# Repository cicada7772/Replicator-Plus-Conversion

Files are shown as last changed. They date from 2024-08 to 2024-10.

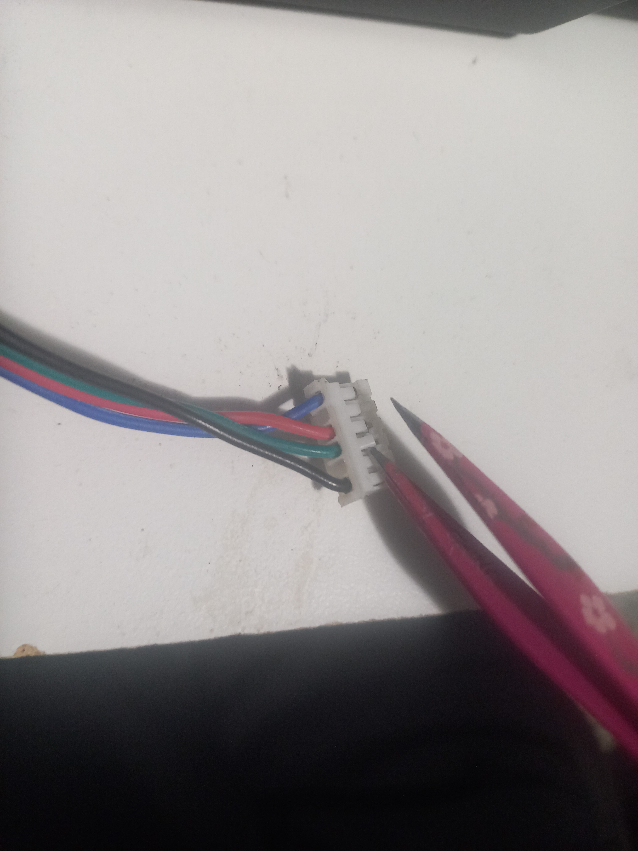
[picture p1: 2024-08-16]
Images/IMG_20240813_204058.jpg

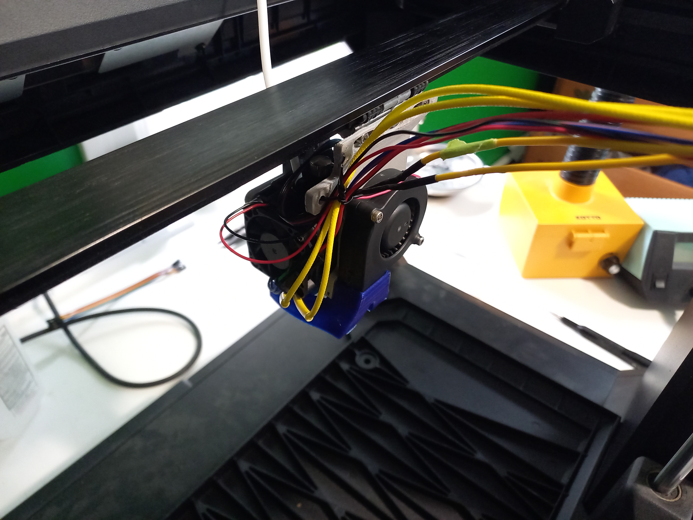
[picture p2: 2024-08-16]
Images/IMG_20240816_153703.jpg

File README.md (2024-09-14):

## Replicator Plus Conversion
This project converts a Makerbot Replicator Plus into a standard, reliable, and fast machine. 

The design goals of this project are:
* Increased reliability
* Use of standard parts
* Minimal disassembly
* Keeping the build process as simple as possible
* Keeping the budget low
* Thorough assembly instructions

Check out the wiki of this repo for details here:
https://github.com/cicada7772/ReplicatorPlusConversion/wiki

Some similar projects:

* https://github.com/mikedaf/Makerbot-Replicator-Plus-Klipper-Conversion
* https://github.com/rolohaun/Replicator5-Klipper

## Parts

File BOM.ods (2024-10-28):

 | ITEM | QTY | Price (USD)
Replicator++
Components | E3D Hemera XS Extruder --> Direct, 12V ← ( SKU:HEMERA-XS-175-COLD-D-12V) | 1 | 127.22
 | E3D Revo Starter Hotside Packs → 12V, 104NT ← (SKU:REVO-HOT-KIT-12V) | 1 | 51.93
 | BTT SKR MINI E3 V3.0 mainboard | 1 | 33.98
 | BL-touch style probe (ex: BIQU Microprobe V2.0) (recommended) | 1 | 18.99
 |  |  | 232.12 | ← Total(USD)
Materials | AWG16 stranded wire | x
 | AWG22 stranded wire | x
 | Stepper cables (1 meter) | 3
 | M3*4 SHCS | 8
 | M3*20 SHCS | 4
 | M3*8 SHCS | 3
 | M3*5 SHCS | 4
 | M3 Hexnuts | 2
Replicator#
Components | E3D Hemera XS Extruder → Direct, 24V ← (SKU:HEMERA-XS-175-COLD-D-24V) | 1 | 127.22
 | Revo Starter Hotside Packs → 24V, 104NT ← (SKU:REVO-HOT-KIT-24V) |  | 51.93
 | BTT SKR MINI E3 V3.0 mainboard | 1 | 33.98
 | omrn TL-Q5MC2-Z probe | 1 | 20
 | Power inlet w/ switch (BIQU recommended) | 1 | 4.9
 | Meanwell LRS-350-24 350W 24V power supply | 1 | 29.13
 | 200x300mm PEI spring steel sheet | 1 | 25
 | Mk2a 200x300mm 24V | 1 | 30
 |  |  | 322.16 | ← Total(USD)
Materials | AWG16 stranded wire | x
 | AWG22 stranded wire | x
 | Stepper cables (1 meter) | 3
 | M3*4 SHCS | 8
 | M3*5 SHCS | 4
 | M3*8 SHCS | 3
 | M3*16 SHCS | 4
 | M3*20 SHCS | 4
 | M3 Hexnuts | 8
 | Nylon washers M3x6x1mm | 8
 | M3 10mm spacers | 4

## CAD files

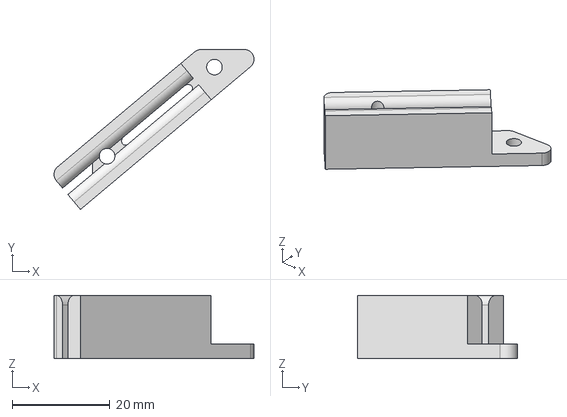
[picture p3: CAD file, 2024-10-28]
CAD/STEP/rpi-mount-clip.stp
41.0 x 32.8 x 13.0 mm

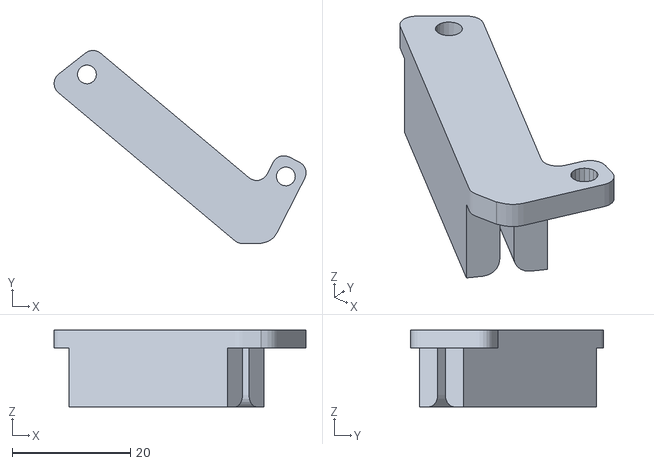
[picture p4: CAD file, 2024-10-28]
STLs/Electronics_skr-mini-mount-clip_4.stl
42.6 x 32.6 x 13.0

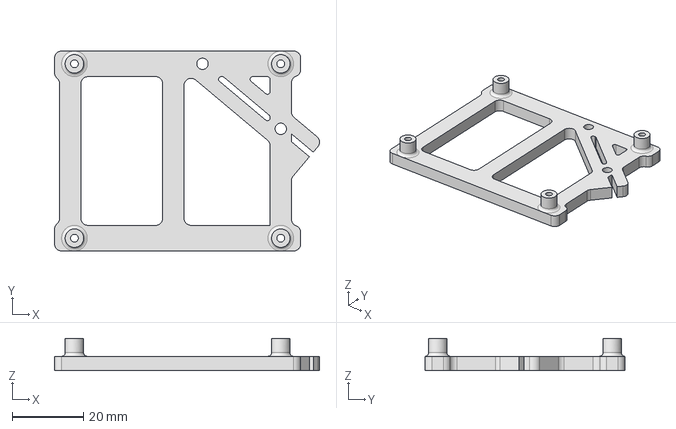
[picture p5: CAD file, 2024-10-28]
CAD/STEP/rpi-mount.stp
74.5 x 56.2 x 9.00 mm

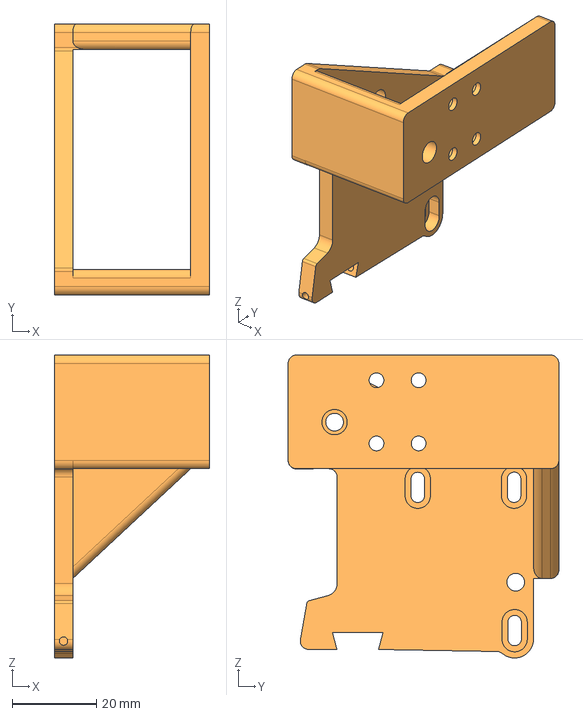
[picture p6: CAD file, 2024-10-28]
CAD/STEP/mount-2.stp
36.9 x 64.3 x 71.9 mm

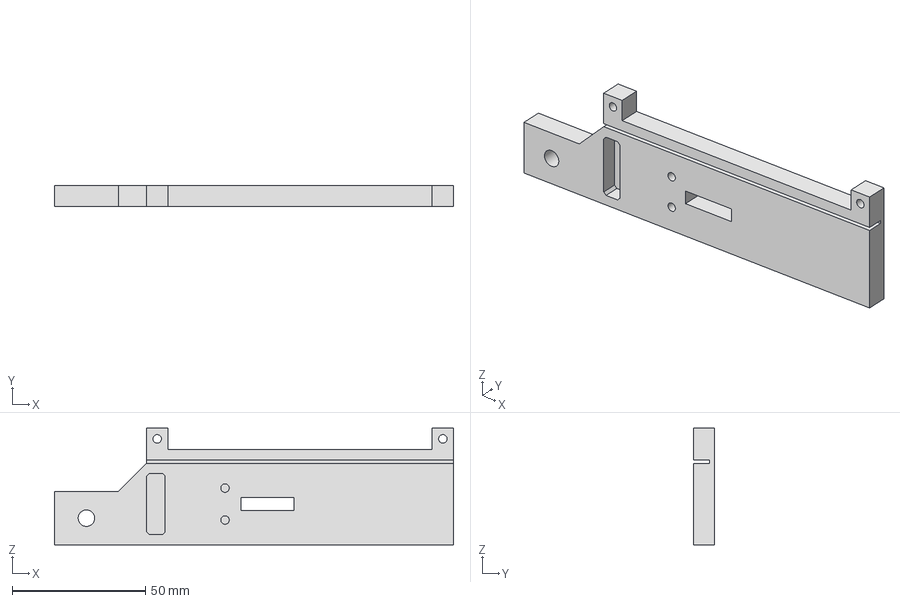
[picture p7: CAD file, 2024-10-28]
CAD/STEP/bowden.stp
150.0 x 8.00 x 43.8 mm

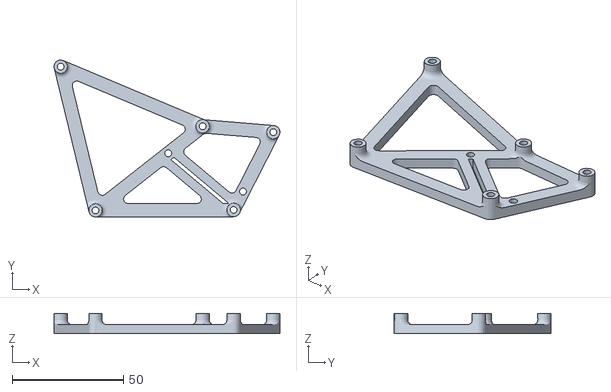
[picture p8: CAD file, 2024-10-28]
STLs/Electronics_skr-mini-mount_2.stl
101.7 x 70.7 x 9.00

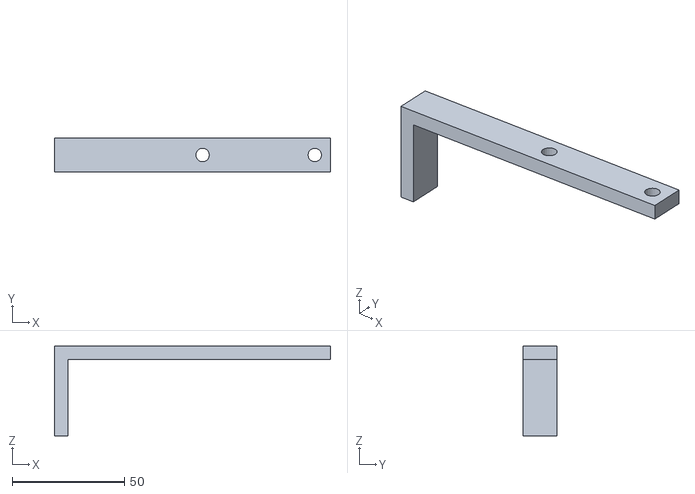
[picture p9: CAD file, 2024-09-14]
STLs/PSU-jig.stl
123.0 x 15.0 x 40.0

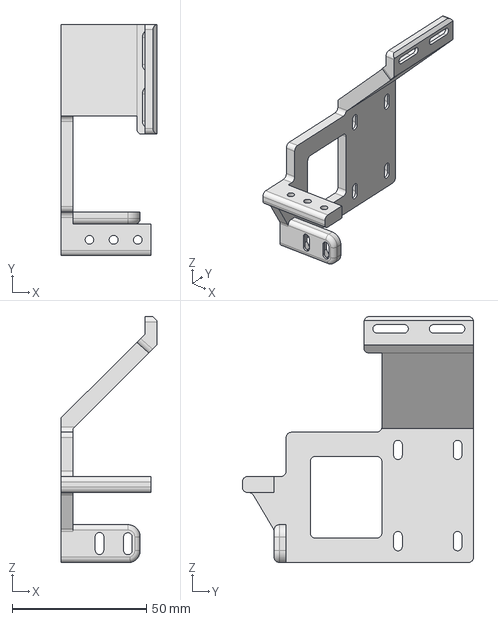
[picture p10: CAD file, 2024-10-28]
CAD/STEP/mount-1.stp
35.7 x 86.2 x 91.7 mm

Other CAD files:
STLs/Electronics_rpi-mount_1.stl
STLs/Electronics_rpi-mount-clip_3.stl
CAD/STEP/skr-mini-mount-clip.stp
CAD/STEP/skr-mini-mount.stp
CAD/Inventor/Electronics.iam
CAD/Inventor/Hemera_XS_Reference_CAD.ipt
CAD/Inventor/Mainboard-spacer.ipt
CAD/Inventor/OldVersions/Electronics.0006.iam
CAD/Inventor/OldVersions/backwall.0007.ipt
CAD/Inventor/OldVersions/bed-small.0007.iam
CAD/Inventor/OldVersions/bed-small.0008.ipt
CAD/Inventor/OldVersions/eddy.0003.ipt
CAD/Inventor/OldVersions/hemera-xs-duct-mount-v2.0004.ipt
CAD/Inventor/OldVersions/hotend-new.0014.iam
CAD/Inventor/OldVersions/mount-1.0015.ipt
CAD/Inventor/OldVersions/rpi-mount.0005.ipt
CAD/Inventor/OldVersions/skr-mini-mount.0005.ipt
CAD/Inventor/backwall.ipt
CAD/Inventor/bolts reference.ipt
CAD/Inventor/eddy.ipt
CAD/Inventor/hemera-mount.ipt
CAD/Inventor/hemera-xs-duct-mount-v2-eddy.ipt
CAD/Inventor/hemera-xs-duct-mount-v2.ipt
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

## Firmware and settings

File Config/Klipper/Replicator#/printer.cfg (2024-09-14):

# This file contains common pin mappings for the BIGTREETECH SKR mini
# E3 v3.0. To use this config, the firmware should be compiled for the
# STM32G0B1 with a "8KiB bootloader" and USB communication/USART.

# The "make flash" command does not work on the SKR mini E3. Instead,
# after running "make", copy the generated "out/klipper.bin" file to a
# file named "firmware.bin" on an SD card and then restart the SKR
# mini E3 with that SD card.

# See docs/Config_Reference.md for a description of parameters.

[include mainsail.cfg]
[include eddy.cfg]

#[safe_z_home]
#home_xy_position: 115,115 # Change coordinates to the center of your print bed
#speed: 50
#z_hop: 10                 # Move up 10mm
#z_hop_speed: 5

#[bed_mesh]
#speed: 120
#horizontal_move_z: 5
#mesh_min: 10, 10
#mesh_max: 190, 220
#probe_count: 5,5

[stepper_x]
step_pin: PB13
dir_pin: PB12
enable_pin: !PB14
microsteps: 16
rotation_distance: 40
position_endstop: 283
position_max: 283
position_min:-52
homing_speed: 20
homing_retract_dist: 0
endstop_pin: tmc2209_stepper_x:virtual_endstop

[tmc2209 stepper_x]
uart_pin: PC11
tx_pin: PC10
uart_address: 0
run_current: 0.80
stealthchop_threshold: 999999
driver_SGTHRS: 69
diag_pin:^PC0

[stepper_y]
step_pin: PB10
dir_pin: PB2
enable_pin: !PB11
microsteps: 16
rotation_distance: 40
#endstop_pin: ^PC1
position_endstop: 189
position_max: 189
position_min: -37
homing_speed: 20
homing_retract_dist: 0
endstop_pin: tmc2209_stepper_y:virtual_endstop

[tmc2209 stepper_y]
uart_pin: PC11
tx_pin: PC10
uart_address: 2
run_current: 0.80
stealthchop_threshold: 999999
driver_SGTHRS: 63
diag_pin:^PC1

[stepper_z]
step_pin: PB0
dir_pin: !PC5
enable_pin: !PB1
microsteps: 16
rotation_distance: 8
endstop_pin: probe:z_virtual_endstop
#position_endstop: 0.0
#endstop_pin: probe:z_virtual_endstop
position_max: 150
position_min: -2

[tmc2209 stepper_z]
uart_pin: PC11
tx_pin: PC10
uart_address: 1
run_current: 0.580
hold_current: 0.500
stealthchop_threshold: 999999

[extruder]
step_pin: PB3
dir_pin: !PB4
enable_pin: !PD1
microsteps: 16
rotation_distance: 8.104769491
nozzle_diameter: 0.400
filament_diameter: 1.750
heater_pin: PC8
sensor_type: EPCOS 100K B57560G104F
sensor_pin: PA0
control: pid
pid_Kp: 21.527
pid_Ki: 1.063
pid_Kd: 108.982
min_temp: 0
max_temp: 300
min_extrude_temp: 0

[tmc2209 extruder]
uart_pin: PC11
tx_pin: PC10
uart_address: 3
run_current: 0.650
hold_current: 0.500
stealthchop_threshold: 999999

[heater_bed]
heater_pin: PC9
sensor_type: ATC Semitec 104GT-2
sensor_pin: PC4
control: pid
pid_Kp: 54.027
pid_Ki: 0.770
pid_Kd: 948.182
min_temp: 0
max_temp: 130

#[heater_fan controller_fan]
#pin: PB15
#heater: heater_bed
#heater_temp: 45.0

[heater_fan nozzle_cooling_fan]
pin: PC7

[fan]
pin: PC6

[mcu]
serial: /dev/serial/by-id/usb-Klipper_stm32g0b1xx_3E0012001150415833323520-if00
# serial: /dev/ttyAMA0
# restart_method: command

[printer]
kinematics: corexy
max_velocity: 800
max_accel: 7000
max_z_velocity: 5
max_z_accel: 100

[board_pins]
aliases:
    # EXP1 header
    EXP1_1=PB5,  EXP1_3=PA9,   EXP1_5=PA10, EXP1_7=PB8, EXP1_9=<GND>,
    EXP1_2=PA15, EXP1_4=<RST>, EXP1_6=PB9,  EXP1_8=PD6, EXP1_10=<5V>

[gcode_macro _HOME_X]
gcode:
    # Always use consistent run_current on A/B steppers during sensorless homing
    {% set RUN_CURRENT_X = printer.configfile.settings['tmc2209 stepper_x'].run_current|float %}
    {% set RUN_CURRENT_Y = printer.configfile.settings['tmc2209 stepper_y'].run_current|float %}
    {% set HOME_CURRENT = 0.7 %}
    SET_TMC_CURRENT STEPPER=stepper_x CURRENT={HOME_CURRENT}
    SET_TMC_CURRENT STEPPER=stepper_y CURRENT={HOME_CURRENT}

    # Home
    G28 X
    # Move away
    G91
    G1 X-10 F1200
    
    # Wait just a second… (give StallGuard registers time to clear)
    G4 P1000
    # Set current during print
    SET_TMC_CURRENT STEPPER=stepper_x CURRENT={RUN_CURRENT_X}
    SET_TMC_CURRENT STEPPER=stepper_y CURRENT={RUN_CURRENT_Y}
    G90

[gcode_macro _HOME_Y]
gcode:
    # Set current for sensorless homing
    {% set RUN_CURRENT_X = printer.configfile.settings['tmc2209 stepper_x'].run_current|float %}
    {% set RUN_CURRENT_Y = printer.configfile.settings['tmc2209 stepper_y'].run_current|float %}
    {% set HOME_CURRENT = 0.7 %}
    SET_TMC_CURRENT STEPPER=stepper_x CURRENT={HOME_CURRENT}
    SET_TMC_CURRENT STEPPER=stepper_y CURRENT={HOME_CURRENT}

    # Home
    G28 Y
    # Move away
    G91
    G1 Y-10 F1200

    # Wait just a second… (give StallGuard registers time to clear)
    G4 P1000
    # Set current during print
    SET_TMC_CURRENT STEPPER=stepper_x CURRENT={RUN_CURRENT_X}
    SET_TMC_CURRENT STEPPER=stepper_y CURRENT={RUN_CURRENT_Y}
    G90

[homing_override]
axes: xyz
gcode:
  {% set home_all = 'X' not in params and 'Y' not in params and 'Z' not in params %}
  {% if home_all or 'Y' in params %}
    _HOME_Y
  {% endif %}

  {% if home_all or 'X' in params %}
    _HOME_X
  {% endif %}
  
  {% if home_all or 'Z' in params %}
    G1 X164.5 Y85.0 F5000
    M400
    G28 Z0
  {% endif %}

[gcode_macro PRINT_START]
gcode:
  # This part fetches data from your slicer. Such as bed temp, extruder temp, chamber temp and size of your printer.
  {% set target_bed = params.BED|int %}
  {% set target_extruder = params.EXTRUDER|int %}
  {% set x_wait = printer.toolhead.axis_minimum.x|float + 2 %}
  {% set y_wait = printer.toolhead.axis_maximum.y|float - 2 %}
  
  M190 S{target_bed}                              # Sets target temp for the bed
  
  # Homes the printer and sets absolute positioning
  G28                   # Full home (XYZ)
  G90                   # Absolut position

  G1 X{x_wait} Y{y_wait} Z15 F9000                # Goes to center of the bed
  
  # Checks if the bed temp is higher than 90c - if so then trigger a heatsoak
  {% if params.BED|int > 90 %}
    M106 S255                                       # Turns on the PT-fan
  {% endif %}

  # Heats up the nozzle up to target via slicer
  M107                                              # Turns off the PT-fan
  M109 S{target_extruder}                           # Heats the nozzle to your print temp

  BED_MESH_CALIBRATE
  BED_MESH_PROFILE LOAD=default

  # Create a purge line and starts the print
  G1 X5 Y4 Z0.4 F10000                             # Moves to starting point
  G1 X115 E20 F1000       # Purge line

[gcode_macro PRINT_END]
gcode:
  G90
  G1 Z150
  TURN_OFF_HEATERS
  M84

#[mcu rpi]
#serial: /tmp/klipper_host_mcu

#[adxl345]
#cs_pin: rpi:None

#[resonance_tester]
#accel_chip: adxl345
#probe_points:
#    185, 126, 20  

[input_shaper]

[gcode_macro TEST_SPEED]
# Home, get position, throw around toolhead, home again.
# If MCU stepper positions (first line in GET_POSITION) are greater than a full step different (your number of microsteps), then skipping occured.
# We only measure to a full step to accomodate for endstop variance.
# Example: TEST_SPEED SPEED=300 ACCEL=5000 ITERATIONS=10

description: Test for max speed and acceleration parameters for the printer. Procedure: Home -> ReadPositionFromMCU -> MovesToolhead@Vel&Accel -> Home -> ReadPositionfromMCU
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

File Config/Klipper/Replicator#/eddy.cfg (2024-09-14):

# The MCU section only applies to the Eddy USB. For Eddy Coil you will use the MCU name of the toolboard that you connected the Eddy Coil to.
[mcu eddy]
serial: /dev/serial/by-id/usb-Klipper_rp2040_45474E621B09B66A-if00 # This is the serial address of your eddy probe. This can be found by using the terminal of your klipper instance (typically through SSH) and using the command ```ls /dev/serial/by-id``` 
restart_method: command

[temperature_sensor btt_eddy_mcu]
sensor_type: temperature_mcu # Sets the type of sensor for Klipper to read
sensor_mcu: eddy # Sets the MCU of the eddy probe tempereature sensor
min_temp: 10 # Sets the minimum tempereature for eddys tempereature sensor to operate
max_temp: 100 # Sets the maximum tempereature for eddys tempereature sensor to operate

[probe_eddy_current btt_eddy]
sensor_type: ldc1612
z_offset: 1.5
#i2c_address:
i2c_mcu: eddy  # This value is good for the Eddy USB but would need to be adjusted for the Eddy Coil according to the MCU you have used.
i2c_bus: i2c0f # This value is good for the Eddy USB but would need to be adjusted for the Eddy Coil according to the I2C bus you have used.
# Measure the offsets below using the method described here: https://www.klipper3d.org/Probe_Calibrate.html#calibrating-probe-x-and-y-offsets
# For a standard Voron stealthburner X carriage mount there should be no need to change the defaults below.
x_offset: -36.5
y_offset: 0

# This section is only relevant for Eddy USB. Comment it out for Eddy Coil.
[temperature_probe btt_eddy]
sensor_type: Generic 3950
sensor_pin: eddy:gpio26
horizontal_move_z: 2

[bed_mesh]
horizontal_move_z: 2
speed: 200
# For the mesh dimensions below, the coordinates need to be reachable by the center of the probe. To calculate coordinates that will work, use the formula below:
# mesh x min = position_min_x + greater_of (15mm or x_offset) <--- in this term, only consider the x offset if it is positive, ignore if negative.
# mesh y min = position_min_y + greater_of (15mm or y_offset) <--- in this term, only consider the y offset if it is positive, ignore if negative.
# mesh x max = position_max_x - greater_of (15mm or |x_offset|) <--- in this term, only consider the x offset if it is negative, ignore if positive.
# mesh y max = position_max_y - greater_of (15mm or |y_offset|) <--- in this term, only consider the y offset if it is negative, ignore if positive.
# Example: Consider that you have a 300 x 300 bed with the max x and y positions being 300 and the min being 0. Your probe offsets are -20 for X and 10 for Y
# For mesh x min we ignore the x offset term because it is negative. Therefore mesh x min = 15
# For mesh y min we do not ignore the y offset term because it is positive but it is less than 15 so we use 15. Therefore mesh y min = 15
# For mesh x max we do not ignore the x offset term because it is negative. It is also greater than 15. Therefore mesh x max = 280
# For mesh y max we ignore the y offset term because it is positive but it is less than 15 so we use 15. Therefore mesh y max = 285
# The final result would be mesh_min: 15, 15 mesh_max: 280, 285
mesh_min: 15, 15  # modify these according to the above guide. If the probe cannot reach then you will get a klipper error when trying to scan a bed mesh.
mesh_max: 246.5, 155 # modify these according to the above guide. If the probe cannot reach then you will get a klipper error when trying to scan a bed mesh.
probe_count: 9, 9
algorithm: bicubic
#scan_overshoot: 8  #uncomment this section if you still have room left over on the X axis for some scan overshoot to product smoother movements and more accurate scanning. Uncommenting this should be fine if you are using a standard voron mount.

# Uncomment this if you are using Eddy as the probe AND the homing endstop
#[safe_z_home]
#home_xy_position: 132.5, 86 # Choose an X,Y position that is in the center of your bed. For a 300x300 machine that will be 150, 150. Use the same principle to calculate your bed center.
#z_hop: 10
#z_hop_speed: 25
#speed: 200

###############################Macros and related################################
#This secton contains macros and related config sections. Some should be used, others are optional. Read the comment above each one to find out whether or not to uncomment it for your installation.


# Uncomment this if you are using Eddy as the probe AND the homing endstop AND would like to use the beta z-offset control
#[save_variables]
#filename: ~/printer_data/config/variables.cfg



# Uncomment this if you are using Eddy as the probe AND the homing endstop
[force_move]
enable_force_move: True # Allows a user to move the z axis down if they have no other means of homing Z and need to calibrate the Eddy.



# Uncomment this if you are using Eddy as the probe AND the homing endstop AND would like to use the beta z-offset control
#[delayed_gcode RESTORE_PROBE_OFFSET]
#initial_duration: 1.
#gcode:
#  {% set svv = printer.save_variables.variables %}
#  {% if not printer["gcode_macro SET_GCODE_OFFSET"].restored %}
#    SET_GCODE_VARIABLE MACRO=SET_GCODE_OFFSET VARIABLE=runtime_offset VALUE={ svv.nvm_offset|default(0) }
#    SET_GCODE_VARIABLE MACRO=SET_GCODE_OFFSET VARIABLE=restored VALUE=True
#  {% endif %}



# Uncomment this if you are using Eddy as the probe AND the homing endstop
# Take note of the lines that should only be used if you have a KNOMI installed.
#[gcode_macro G28.1]
#rename_existing: G28.1
#gcode:
  #SET_GCODE_VARIABLE MACRO=_KNOMI_STATUS VARIABLE=homing VALUE=True # Uncomment this if using a KNOMI and then remove the G28 macro from the KNOMI.cfg
  #G28.1 {rawparams}
#  {% set home_all = 'X' not in params and 'Y' not in params and 'Z' not in params %}
#
#  {% if home_all or 'X' in params %}
#    _HOME_X
#  {% endif %}
#  
#  {% if home_all or 'Y' in params %}
#    _HOME_Y
#  {% endif %}
#  {% if not rawparams or (rawparams and 'Z' in rawparams) %}
#    PROBE
#    SET_Z_FROM_PROBE
#  {% endif %}
  #SET_GCODE_VARIABLE MACRO=_KNOMI_STATUS VARIABLE=homing VALUE=False # Uncomment this if using a KNOMI and then remove the G28 macro from the KNOMI.cfg



# Uncomment this if you are using Eddy as the probe AND the homing endstop
[gcode_macro SET_Z_FROM_PROBE]
gcode:
    {% set cf = printer.configfile.settings %}
    SET_GCODE_OFFSET_ORIG Z={printer.probe.last_z_result - cf['probe_eddy_current btt_eddy'].z_offset + printer["gcode_macro SET_GCODE_OFFSET"].runtime_offset}



# Uncomment this if you are using Eddy as the probe AND the homing endstop AND would like to use the beta z-offset control
#[gcode_macro Z_OFFSET_APPLY_PROBE]
#rename_existing: Z_OFFSET_APPLY_PROBE_ORIG
#gcode:
#  SAVE_VARIABLE VARIABLE=nvm_offset VALUE={ printer["gcode_macro SET_GCODE_OFFSET"].runtime_offset }



# Uncomment the lines in this macro if you are using Eddy as the probe AND the homing endstop AND would like to use the beta z-offset control
[gcode_macro SET_GCODE_OFFSET]
rename_existing: SET_GCODE_OFFSET_ORIG
variable_restored: False  # Mark whether the var has been restored from NVM
variable_runtime_offset: 0
gcode:
#  {% if params.Z_ADJUST %}
#    SET_GCODE_VARIABLE MACRO=SET_GCODE_OFFSET VARIABLE=runtime_offset VALUE={ printer["gcode_macro SET_GCODE_OFFSET"].runtime_offset + params.Z_ADJUST|float }
#  {% endif %}
#  {% if params.Z %}
#    {% set paramList = rawparams.split() %}
#    {% for i in range(paramList|length) %}
#      {% if paramList[i]=="Z=0" %}
#        {% set temp=paramList.pop(i) %}
#        {% set temp="Z_ADJUST=" + (-printer["gcode_macro SET_GCODE_OFFSET"].runtime_offset)|string %}
#        {% if paramList.append(temp) %}{% endif %}
#      {% endif %}
#    {% endfor %}
#    {% set rawparams=paramList|join(' ') %}
#    SET_GCODE_VARIABLE MACRO=SET_GCODE_OFFSET VARIABLE=runtime_offset VALUE=0
#  {% endif %}
  SET_GCODE_OFFSET_ORIG { rawparams }



# This macro automates a lot of the frequency mapping process and simplifies the steps significantly.
[gcode_macro PROBE_EDDY_CURRENT_CALIBRATE_AUTO]
gcode:
  BED_MESH_CLEAR
  G28 X Y
  G1 X{ printer.toolhead.axis_maximum.x/2 } Y{ printer.toolhead.axis_maximum.y/2 } F6000
  {% if 'z' not in printer.toolhead.homed_axes %}
    SET_KINEMATIC_POSITION Z={ printer.toolhead.axis_maximum.z-1 } # Allows the user to work it down until it touches.
  {% endif %}
  PROBE_EDDY_CURRENT_CALIBRATE {rawparams}



#This macro is optional but useful if you want to run a rapid scan before each print. Simply uncomment it and add BED_MESH_SCAN to your print start code.
[gcode_macro BED_MESH_CALIBRATE]
rename_existing: BTT_BED_MESH_CALIBRATE
gcode:
  #SET_GCODE_VARIABLE MACRO=_KNOMI_STATUS VARIABLE=probing VALUE=True #Only uncomment this line if using a KNOMI and then remove the BED_MESH_CALIBRATE macro from KNOMI.cfg
  BTT_BED_MESH_CALIBRATE METHOD=rapid_scan
  #SET_GCODE_VARIABLE MACRO=_KNOMI_STATUS VARIABLE=probing VALUE=False #Only uncomment this line if using a KNOMI and then remove the BED_MESH_CALIBRATE macro from KNOMI.cfg

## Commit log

2024-07-17 update names
    [bed-oops.iam, bed-oops.ipt, bed-plate_oops.ipt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]
2024-07-18 300x200mm bed cad
    [bed-heater.ipt, bed-interface.ipt, bed-plate.ipt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]
2024-07-18 updates to hotend
    [eddy.ipt, hemera-mount.ipt, hemera-xs-duct-mount-v2-eddy.ipt]
2024-07-18 oops that wouldnt have worked
    [eddy.ipt, hemera-mount.stl, hemera-xs-duct-mount-v2-eddy.ipt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]
2024-07-20 resize mounting holes
    [Hemera_XS_Reference_CAD.0001.ipt, Hemera_XS_Reference_CAD.ipt, hotend.0021.iam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]
2024-07-24 more material
    [Hemera-mount-1.stl, rails-bolts.0009.ipt, rails-bolts.0010.ipt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]
2024-08-02 update mounts from empirical data
    [Hemera-mount-1.stl, hemera-duct-mount-2.stl, hemera-xs-duct-mount-v2-eddy.0011.ipt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]
2024-08-13 update mount to fix angle of hotend
    [hemera-duct-mount-2.stl, hemera-xs-duct-mount-v2-eddy.0012.ipt, hemera-xs-duct-mount-v2-eddy.0013.ipt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]
2024-08-14 add ziptie wire mount
    [hemera-duct-mount-2.stl, hemera-xs-duct-mount-v2-eddy.0013.ipt, hemera-xs-duct-mount-v2-eddy.0014.ipt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]
2024-08-14 actually fix the problem this time
    [hemera-duct-mount-2.stl, hemera-xs-duct-mount-v2-eddy.0014.ipt, hemera-xs-duct-mount-v2-eddy.0015.ipt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]
2024-08-16 docs updates
    [hemera-xs-duct-mount-v2-eddy.0015.ipt, hemera-xs-duct-mount-v2-eddy.0016.ipt, hemera-xs-duct-mount-v2-eddy.ipt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]
2024-08-19 new toolhead
    [Hemera_XS_Reference_CAD.ipt, bed-heater.ipt, bed-interface.ipt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]
2024-09-14 bltouch mount
    [eddy.0003.ipt, eddy.ipt, hemera-xs-duct-mount-v2.0004.ipt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]
2024-09-14 backwall
    bowden wall
    update skr mount
    [Hemera-mount-1.stl, Mainboard-spacer.ipt, backwall.0004.ipt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]
2024-09-14 update skr mount
    make fit tighter
    [mainboard-mount.stl, skr-mini-mount.0002.ipt, skr-mini-mount.0003.ipt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]
2024-09-14 update BOM
    [BOM.ods]
2024-09-21 Config upate
    [eddy.cfg, printer-rplusplus-bltouch.cfg, printer-rplusplus-endstop.cfg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]
2024-10-12 Rpi Mount
    [rpi-mount.ipt, rpi-mount.stl]
2024-10-13 edit to backwall, depreciating bed CAD
    [backwall.0004.ipt, backwall.0007.ipt, backwall.ipt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]
2024-10-13 Raspberry pi mount update
    [rpi-mount.0001.ipt, rpi-mount.ipt, rpi-mount.stl]
2024-10-13 Electronic mounts refactor
    [Electronics.iam, mainboard-mount.stl, rpi-mount.0001.ipt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]
2024-10-14 rpi mount v3
    [Electronics.0001.iam, Electronics.iam, Part1.ipt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]
2024-10-19 shift rpi mount for usb connector clearance
    [rpi-mount.0003.ipt, rpi-mount.0004.ipt, rpi-mount.ipt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]
2024-10-28 update electronics mounts, add step variants of all parts
    [Electronics.0001.iam, Electronics.0006.iam, Electronics.iam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]
